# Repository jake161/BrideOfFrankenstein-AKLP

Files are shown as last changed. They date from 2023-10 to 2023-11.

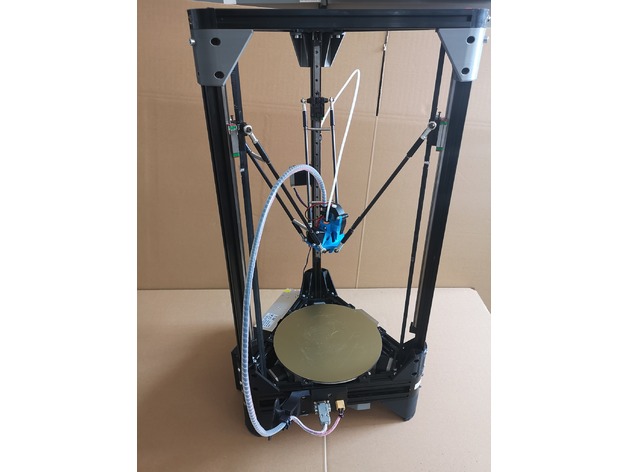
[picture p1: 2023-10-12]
STLs/Anycubic_Kossel_Linear_Plus__Light_weight_Effector_upgrade__E3D_V6__Volcano_too__and_5015_blower_4329200/images/featured_preview_95667094_4322474284432976_2573437162724786176_o.jpg

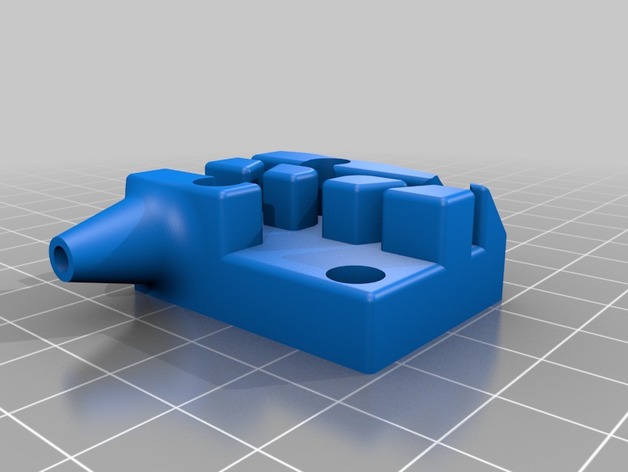
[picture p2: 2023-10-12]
STLs/Carriages_for_Anycubic_Delta_Kossel_Linear_Plus_2281894/images/Carriage_53mm.jpg

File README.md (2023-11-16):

# Bride of Frankenstein
## Anycubic Kossel Linear Plus Refresh and Klipper Conversion

_Everything here is work in progress, but hopefully it can be of some use!_

This repo is a dump/backup of my current Anycubic Kossel Klipper configuration which I affectionately call:

**Bride of Frankenstein (_BOF_)**

After swapping out the main board a few times, cannibalizing parts, and losing my configs, I had to cobble this monster back into something usable.

My current goal is to produce a bill of materials so that this machine can be reproduced. I believe the original Anycubic KLP was a great starter delta machine and hope it continues to get some use!

In pursuit of that goal, I've added some hardware and printable mods that really improve the experience. I'll include the STLs, and I'll try to properly credit and source their creators later on. Thank you for your work!

I've included the current printer.cfg, custom macros (a few of which are adopted from people on the klipper discord / lots of googling), and my PrusaSlicer configs.

## TODO:
- Create BOM for stock AKLP with quality of life upgrades (BOFV2)
- Create BOM for better start configuration with more substantial changes (BOFV3)

## CAD Attribution:

- [Original CAD by SPIKELEE](https://cults3d.com/:991294)

## STLs Attribution:

- [Improved Carriages (50mm version)](https://www.thingiverse.com/thing:2281894/files)
- [Upgraded Effector](https://www.thingiverse.com/thing:4329200)
- [Voron M4 Extruder](https://github.com/VoronDesign/Mobius-Extruder)
- [Glass Bed Clips](https://www.printables.com/model/137809-anycubic-kossel-linear-plus-glass-bed-clamp)
- [Corner Reinforcements](https://www.thingiverse.com/thing:2620272)
- [Top Mount Tensioners](https://www.thingiverse.com/thing:2827665)
- [Side Mounted Spool Holder](https://www.thingiverse.com/thing:2909802)

## Mods Currently in Use:

- [TMC2209s](https://www.amazon.com/BIGTREETECH-TMC2209-Stepper-Stepstick-Motherboard/dp/B07ZPYKL46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) _(I might post a guide for this since the resources I used in the past are outdated)_
- E3D V6 Clone _(Gulfcoast Robotics)_
- [Ultrabase](https://www.aliexpress.us/item/2251832729128038.html?gatewayAdapt=glo2usa4itemAdapt) _(I DO NOT recommend this bed, but it is currently what I am using. Adhesion sucks)_

## Macros worth pointing out:

- [PURGE_ARC](https://github.com/whyme12/Klipper_Macro_Collection)
- M600 _(If I can find the source I'll link it)_

## A few issues to note:

*Due to the modified effector I am currenty using, you can't use the fully radius of the build area. It's currently locked at R100mm for the Delta Radius, but delta calibrate says it's 134mm. To compensate, my PrusaSlicer profile is locked at D200mm. Also the PURGE_ARC macro has a 35mm offset to not exceed max dimensions.*

*Retraction is a bit out of whack at the moment. Currently running an Voron Mobius 4 Extruder on the worlds worst nema 17 (ripped from a tevo tarantula). My accel values are a bit off to not generate too much noise while printing. Although, I may try to drop retract speed even further. Update: I ran a slow retraction test. I believe the issue to actually be pressure advance. The filament travel is quite long so my PA values are really aggressive. I'll shorten it and retune.* 

*Tip: Something I learned the hard way is that you CANNOT use BED_MESH_CALIBRATE while running DELTA_CALIBRATE. Delta calibrate compensates for any innacuracies in your build by assuming a planar build surface. This means running a bed mesh will just exagerate imperfections and wildly throw off kinematics. (I've literally watched the effector fly away from the bed on the first layer)*

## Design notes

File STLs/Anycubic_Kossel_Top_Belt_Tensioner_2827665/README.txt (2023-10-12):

Anycubic Kossel Top Belt Tensioner by Atziano on Thingiverse: https://www.thingiverse.com/thing:2827665

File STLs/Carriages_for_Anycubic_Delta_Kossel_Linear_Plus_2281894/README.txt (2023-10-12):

Carriages for Anycubic Delta Kossel Linear Plus by theinternal on Thingiverse: https://www.thingiverse.com/thing:2281894

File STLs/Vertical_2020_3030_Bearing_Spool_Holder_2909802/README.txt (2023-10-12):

Vertical 2020/3030 Bearing Spool Holder by Hultis on Thingiverse: https://www.thingiverse.com/thing:2909802

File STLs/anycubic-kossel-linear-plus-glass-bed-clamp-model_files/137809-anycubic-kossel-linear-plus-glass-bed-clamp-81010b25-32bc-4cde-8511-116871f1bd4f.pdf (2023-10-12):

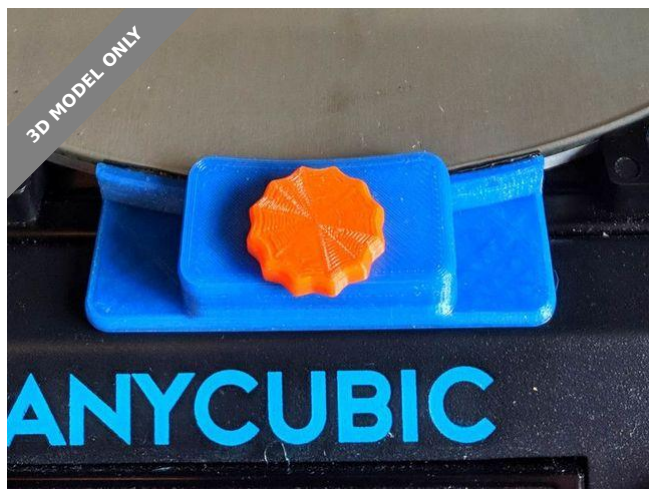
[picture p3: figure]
3D MODEL ONLY

# Summary

Update 27Jan20 In printing something wider than usual, I discovered that

the underside of my part cooling duct hit the...

3D Printers (https://www.printables.com/model?categoryId=1) | > | 3D Printers - Upgrades (https://www.printables.com/model?categoryId=2)
Tags: anycubickossel | linearplus | glassbedclamp

### Update 27Jan20

In printing something wider than usual, I discovered that the underside of

my part cooling duct hit the clamp bolt head on one of the side clamps (at

a radius of 110mm). I've redesigned the clamp bolt head to be a lever. This

alleviates two problems, firstly the width of the bolt head is less on the

build plate side of the clamp and a collision is less likely (not impossible - it

depends what you've set as your printable radius and which part cooling

duct you're using (I'm using Facocero's Thingiverse 3850300). If the

printable radius is less than 110mm, collision is avoided - the Anycubic

default seems to be 105mm), and secondly, David_J's problem of the bolt

being a little too tight to undo comfortably, because now the bolt head is

the shape of a small spanner / wrench and gives a little extra leverage. As

a feature, when tightened, the lever parks with its protruberance

perpendicular to the build plate, as shown in the photo. This is now version

## PeterH1500 (https://www.printables.com/social/222565/about)

# Anycubic Kossel Linear Plus Glass Bed Clamp

VIEW IN BROWSER (https://www.printables.com/model/137809-anycubic-kossel-linear-plus-glass-bed-clamp)

updated 12. 4. 2022 | published 22. 2. 2022

1.2, which I printed 3 bolts at a time in orange Sunlu PLA+ with 0.2mm

layers (0.5mm nozzle), 3 perimeters and 10% infill.

### Update 13Nov19

Following from David_J's comment about the clamp screw being difficult to

unscrew, I've produced a design for a small spanner / wrench for those

who have this difficulty. I've printed this in silver Sunlu PLA+ with 0.25mm

layers (0.5mm nozzle), 5 perimeters and 20% infill.

### Update 21Oct19:

I have extended the fixing bolt holes to allow additional, tighter

adjustment towards the build plate (an additional 0.925mm). This is now

version 1.1, and the Onshape link will now take you to this version.

Initial version 31Jul19:

I hadn't found a suitable clamp to hold my borosilicate glass build plate on

my heated bed, so I set about designing one from scratch. I used Onshape

for the original drawing, so if you want to do any adjustments to the

original drawings you can find them with this link:

https://cad.onshape.com/documents/ec0d91ee24f4f9e61d9240a1/w/

4435b4504876d0c24c086cef/e/5444b0fb228acd7783f3b459 (https://cad.onshape.com/documents/ec0d91ee24f4f9e61d9240a1/w/4435b4504876d0c24c086cef/e/5444b0fb228acd7783f3b459)

The Anycubic Kossel Linear Plus has a 240mm diameter build plate held in

place on a triangle formed from 2020 profile aluminium extrusion.

I regularly use my heated build plate at 70°C, so I printed the clamp in

PETG because of it's higher temperature tolerance when compared to PLA

(glass transition at about 80°C versus 60-65°C, but also added a silicone

gasket in the form of self-amalgamating tape, to help insulate the PETG,

just in case I want to use a bed temperature higher than 80°C. I glued this

in place with a clear impact adhesive. If you use the same stuff, don't

allow your gaskets to touch or they will amalgamate and prevent you

removing your clamp!

I printed the clamp bolt/screw in Sunlu PLA+ because the threads are

better defined than with PETG, and the screw doesn't touch anything hot

and so won't melt or distort.

As well as the printed parts, you'll need 2 off M3 x 8mm socket button

screws (these fit in the recess) and M3 T-nuts for each clamp.

# Print Settings

## Printer:

# Model files

Anycubic Kossel Linear Plus (Delta)

## Rafts:

No

## Supports:

No

## Resolution:

0.2mm first layer then 0.15mm

## Infill:

25%

### Filament: Esun (PETG) & Sunlu (PLA+) PETG (blue) & PLA+ (orange)

## Notes:

The degree of infill doesn't appear to be critical.

Category: 3D Printer Parts

## clamp.stl

## spanner.stl

## clamp_bolt.stl

## clamp_bolt_v12.stl

Find source .stl files on Thingiverse.com (https://www.thingiverse.com/thing:3781497)

# License

This work is licensed under a

Creative Commons (4.0 International License)

Attribution—Noncommercial—Share Alike (http://creativecommons.org/licenses/by-nc-sa/4.0/)

### ✖ | Sharing without ATTRIBUTION

✔ | Remix Culture allowed
✖ | Commercial Use
✖ | Free Cultural Works
✖ | Meets Open Definition

## clamp_base_v11.stl

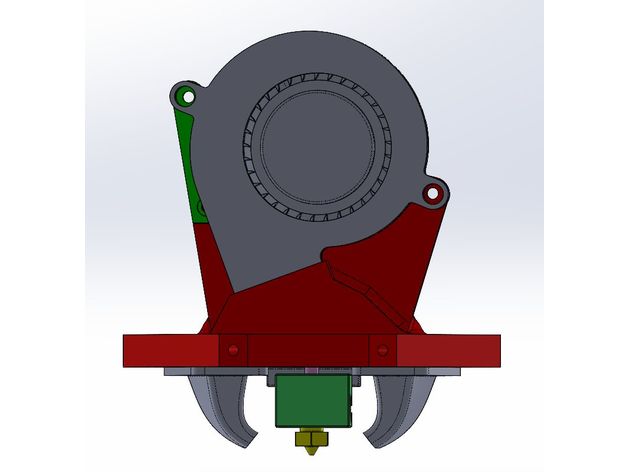
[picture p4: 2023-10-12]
STLs/Anycubic_Kossel_Linear_Plus__Light_weight_Effector_upgrade__E3D_V6__Volcano_too__and_5015_blower_4329200/images/featured_preview_2.jpg

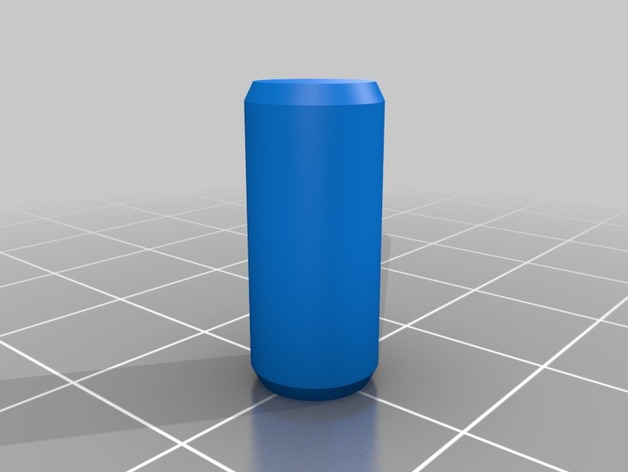
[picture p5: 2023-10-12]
STLs/Vertical_2020_3030_Bearing_Spool_Holder_2909802/images/Pin.jpg

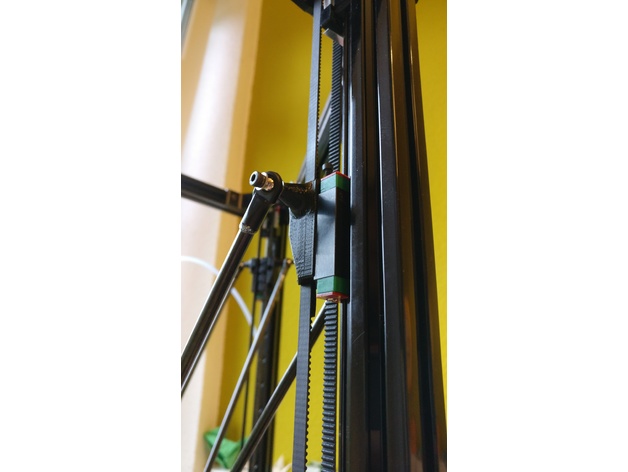
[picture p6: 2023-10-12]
STLs/Carriages_for_Anycubic_Delta_Kossel_Linear_Plus_2281894/images/ce06621213bb93edf30e082a9b9ab08d.jpg

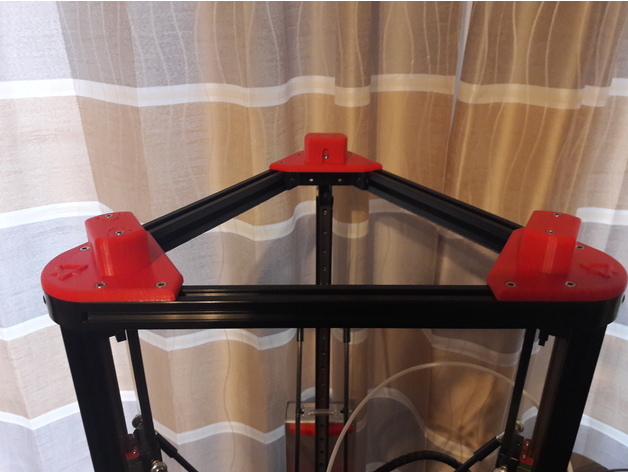
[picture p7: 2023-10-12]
STLs/Anycubic_Kossel_Top_Belt_Tensioner_2827665/images/1eb0ceaca3b0e80c4a3fc1027c2ebc53.jpg

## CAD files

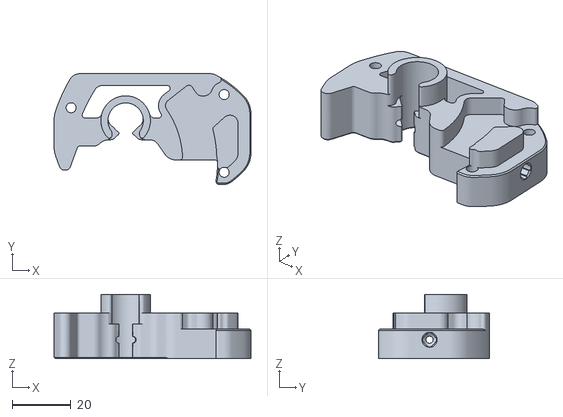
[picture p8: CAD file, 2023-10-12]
STLs/Mobius-Extruder-M4/Mobius-Extruder-M4/STLs/main_body_mirror.stl
66.8 x 37.6 x 21.8

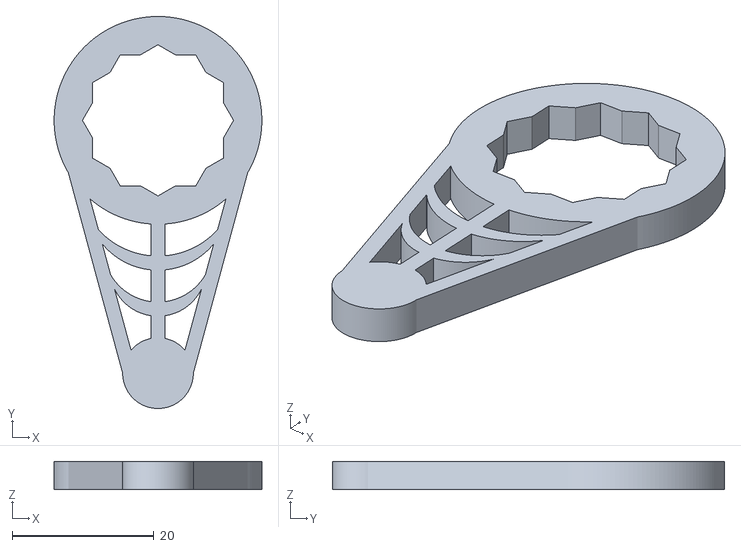
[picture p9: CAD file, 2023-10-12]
STLs/anycubic-kossel-linear-plus-glass-bed-clamp-model_files/spanner.stl
29.4 x 55.4 x 4.00

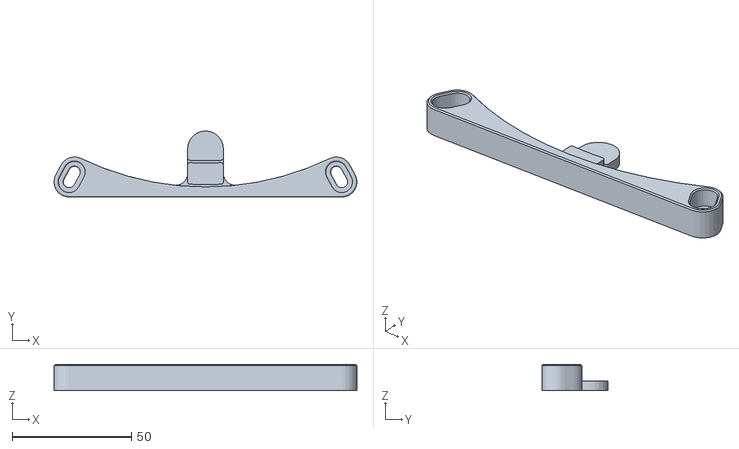
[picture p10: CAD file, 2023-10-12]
STLs/anycubic-kossel-plus-heated-bed-clips-3d-model/files/Anycubic_Plus_Bed_Clip.stl
127.0 x 27.8 x 11.0

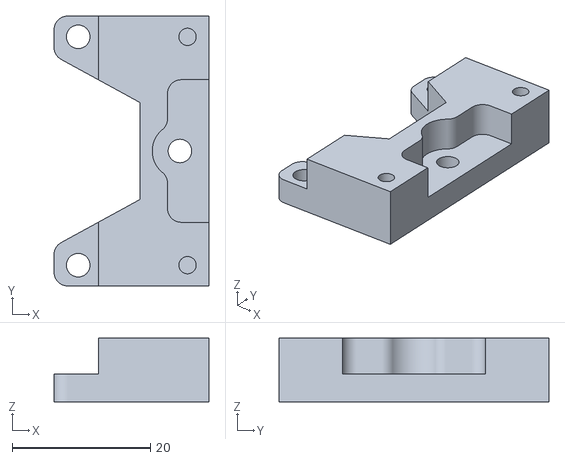
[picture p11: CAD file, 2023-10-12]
STLs/Anycubic_Kossel_Linear_Plus__Light_weight_Effector_upgrade__E3D_V6__Volcano_too__and_5015_blower_4329200/files/volcano_offset_holder_sensor.STL
22.4 x 39.0 x 9.20

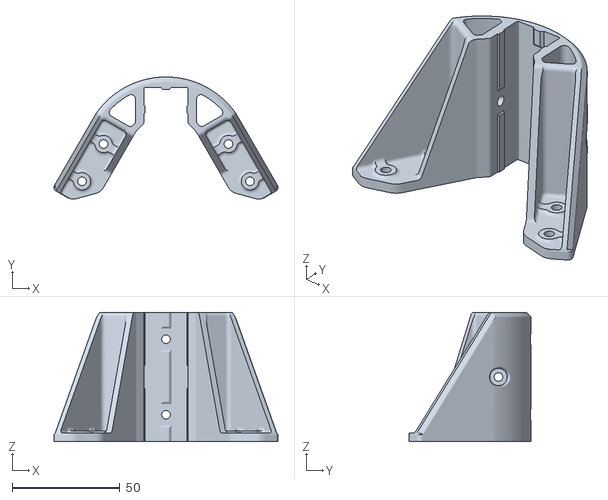
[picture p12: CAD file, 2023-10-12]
STLs/Anycubic_Kossel_Plus_Reinforcement_Corner_-_Escuadr_n_2620272/files/Escuadron_1hole.STL
103.9 x 56.6 x 60.0

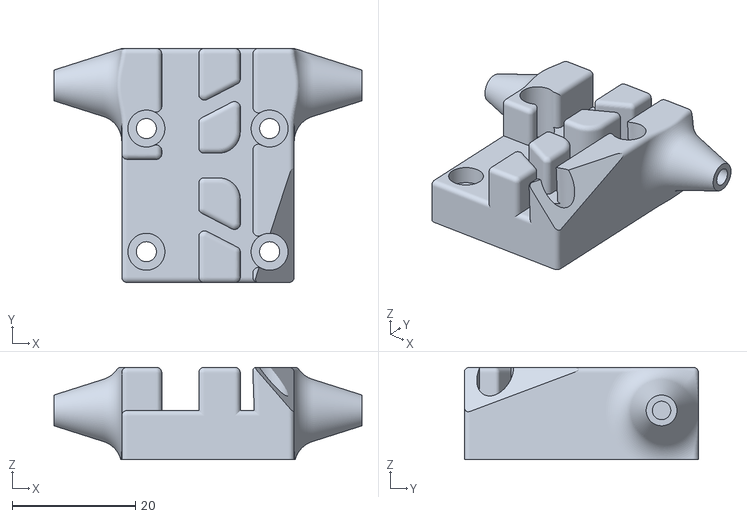
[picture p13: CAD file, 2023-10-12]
STLs/Carriages_for_Anycubic_Delta_Kossel_Linear_Plus_2281894/files/Carriage_50mm.stl
50.0 x 38.0 x 15.0

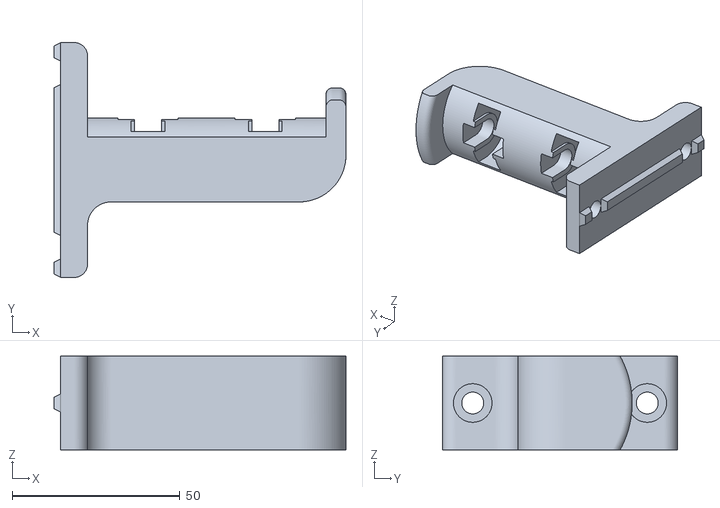
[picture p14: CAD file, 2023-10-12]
STLs/Vertical_2020_3030_Bearing_Spool_Holder_2909802/files/3030_spool_holder.stl
87.0 x 70.0 x 28.0

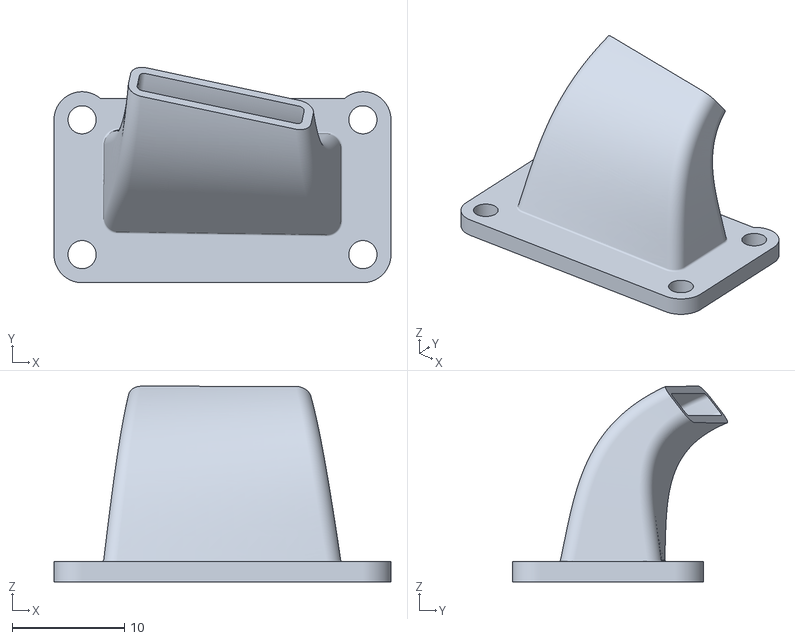
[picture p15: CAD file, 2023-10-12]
STLs/Anycubic_Kossel_Linear_Plus__Light_weight_Effector_upgrade__E3D_V6__Volcano_too__and_5015_blower_4329200/files/fan_jet_L.STL
30.0 x 19.2 x 17.4

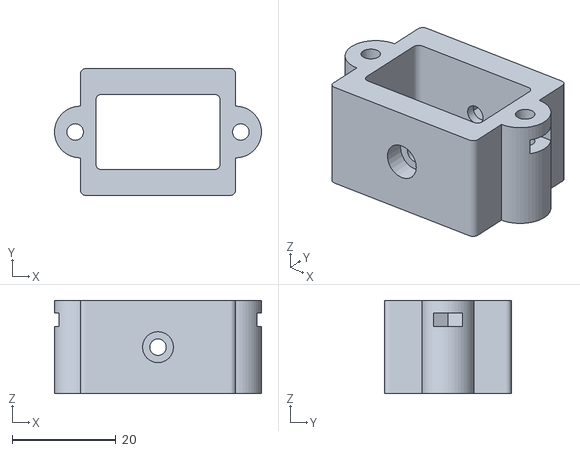
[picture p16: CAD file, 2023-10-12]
STLs/Anycubic_Kossel_Top_Belt_Tensioner_2827665/files/Slider.stl
40.0 x 24.5 x 18.1

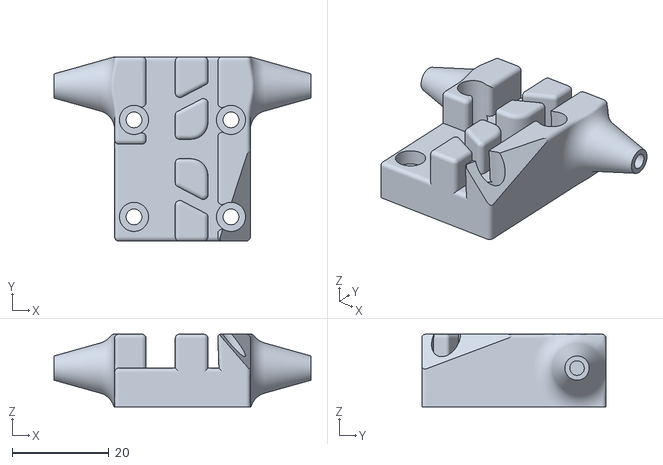
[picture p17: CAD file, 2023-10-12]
STLs/Carriages_for_Anycubic_Delta_Kossel_Linear_Plus_2281894/files/Carriage_53mm.stl
53.0 x 38.0 x 15.0

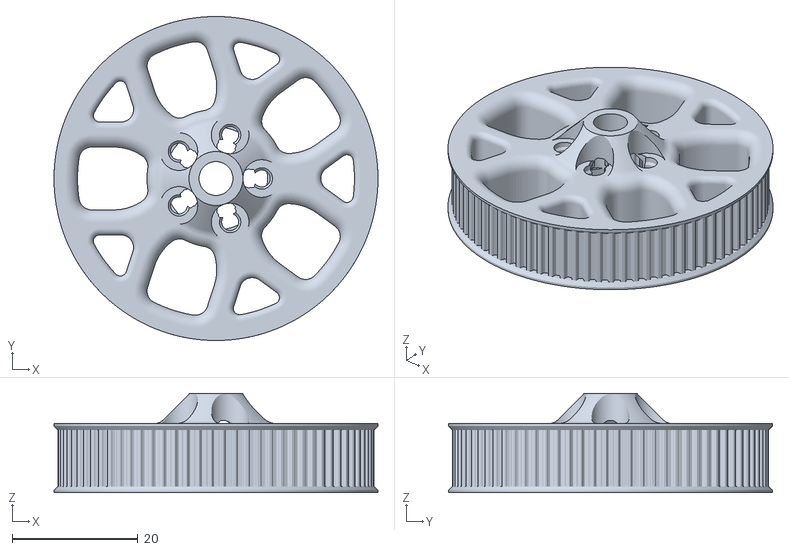
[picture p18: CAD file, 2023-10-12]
STLs/Mobius-Extruder-M4/Mobius-Extruder-M4/STLs/[a]_80t_gear.stl
51.6 x 51.6 x 15.8

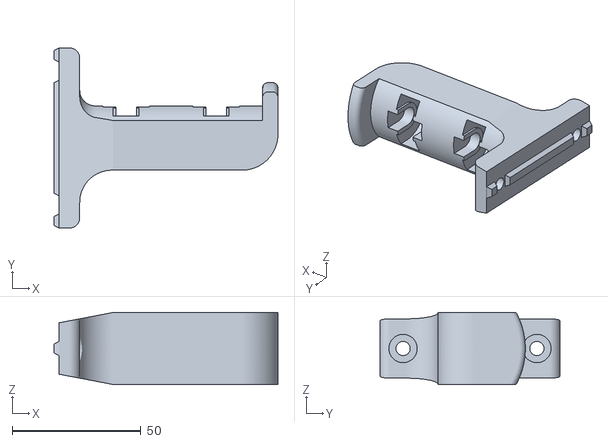
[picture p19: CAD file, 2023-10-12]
STLs/Vertical_2020_3030_Bearing_Spool_Holder_2909802/files/2020_spool_holder.stl
87.0 x 70.0 x 28.0

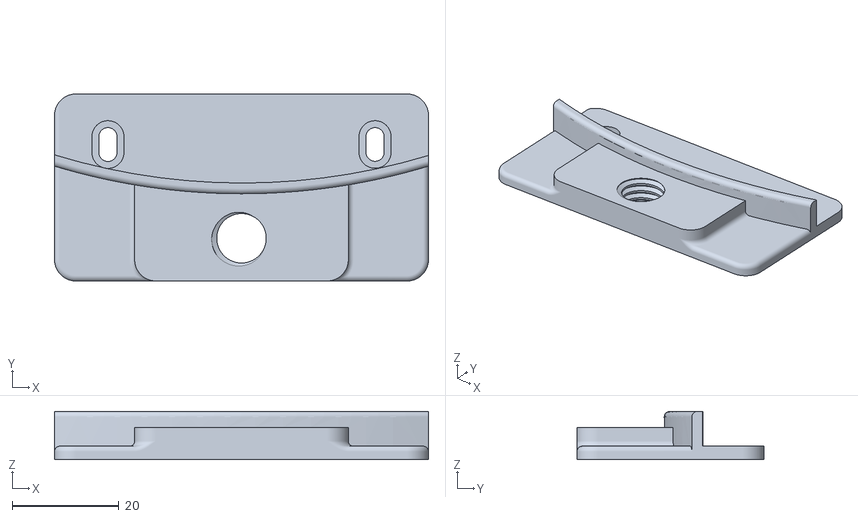
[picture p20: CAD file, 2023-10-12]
STLs/anycubic-kossel-linear-plus-glass-bed-clamp-model_files/clamp_base_v11.stl
70.0 x 35.0 x 9.00

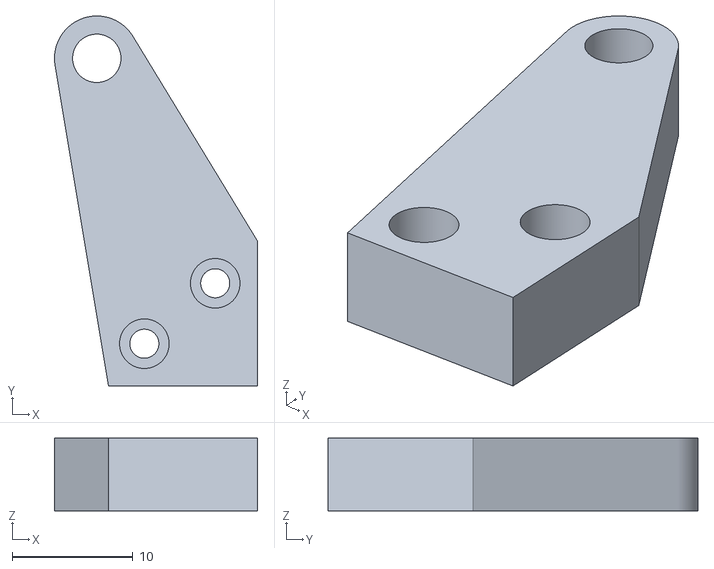
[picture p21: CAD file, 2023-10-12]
STLs/Anycubic_Kossel_Linear_Plus__Light_weight_Effector_upgrade__E3D_V6__Volcano_too__and_5015_blower_4329200/files/5015_blower_holderWithBigger4mmHole.STL
16.8 x 30.6 x 6.00

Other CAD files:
STLs/Mobius-Extruder-M4/Mobius-Extruder-M4/STLs/main_body.stl
STLs/Anycubic_Kossel_Plus_Reinforcement_Corner_-_Escuadr_n_2620272/files/Escuadron_simple_V2.STEP
STLs/Anycubic_Kossel_Plus_Reinforcement_Corner_-_Escuadr_n_2620272/files/Escuadron_2hole.STL
STLs/Anycubic_Kossel_Top_Belt_Tensioner_2827665/files/TopcoverV1.1.stl
STLs/Anycubic_Kossel_Linear_Plus__Light_weight_Effector_upgrade__E3D_V6__Volcano_too__and_5015_blower_4329200/files/5015_blower_holder.STL
STLs/Anycubic_Kossel_Linear_Plus__Light_weight_Effector_upgrade__E3D_V6__Volcano_too__and_5015_blower_4329200/files/fan_jet_R.STL
STLs/Anycubic_Kossel_Linear_Plus__Light_weight_Effector_upgrade__E3D_V6__Volcano_too__and_5015_blower_4329200/files/u_horseshoe.STL
STLs/Anycubic_Kossel_Plus_Reinforcement_Corner_-_Escuadr_n_2620272/files/Escuadron_simple_v2.STL
STLs/Anycubic_Kossel_Top_Belt_Tensioner_2827665/files/TopcoverV1.0.stl
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

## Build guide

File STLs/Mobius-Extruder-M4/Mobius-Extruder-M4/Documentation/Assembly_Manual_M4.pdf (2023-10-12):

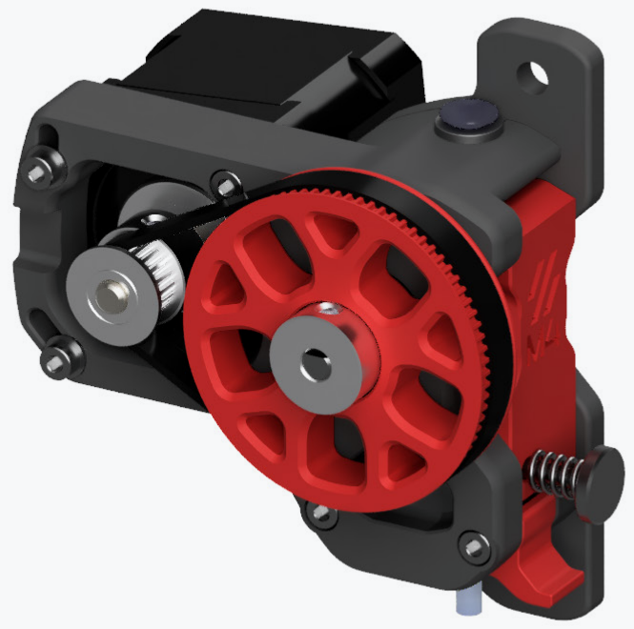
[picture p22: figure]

1

### WWW.VORONDESIGN.COM

VERSION 2020-10-19

# M4 ASSEMBLY MANUAL

## We build space shuttles with gardening tools

so anyone can have a space shuttle of their own.

# VORON

2

INTRODUCTION | WWW.VORONDESIGN.COM

Before you begin on your journey, a word of caution.

In the comfort of your own home you are about to assemble a robot. This
machine can maim, burn, and electrocute you if you are not careful. Please
do not become the first VORON fatality. There is no special Reddit flair for that.

Please, read the entire manual before you start assembly. As you begin wrenching, please check our Discord channels for any tips and questions that may halt your progress.

Most of all, good luck!
THE VORON TEAM

3

INTRODUCTION | WWW.VORONDESIGN.COM

PART PRINTING GUIDELINES
The Voron Team has provided the following print guidelines for you to follow in order to have the best chance at success with your parts. There are often questions about substituting materials or changing printing standards, but we recommend you follow these.

3D PRINTING PROCESS
Fused Deposition Modeling (FDM)

MATERIAL
ABS

LAYER HEIGHT
Recommended: 0.2mm

EXTRUSION WIDTH
Recommended: Forced 0.4mm

INFILL TYPE
Grid, Gyroid, Honeycomb, Triangle or Cubic

INFILL PERCENTAGE
Recommended: 40%

WALL COUNT
Recommended: 4

SOLID TOP/BOTTOM LAYERS
Recommended: 5

PRINT IT FORWARD (PIF)
Often times our community members have issues printing ABS will bootstrap themselves into a VORON using our Print It Forward program. This is a service where approved members with VORON printers can make you a functional set of parts to get your own machine up and running.
Check Discord if you have any interest in having someone help you out.

4

INTRODUCTION | WWW.VORONDESIGN.COM

HOW TO GET HELP
If you need assistance with your build, we’re here to help. Head on over to our Discord group and post your questions. This is our primary medium to help VORON Users and we have a great community that can help you out if you get stuck.

https://discord.gg/voron

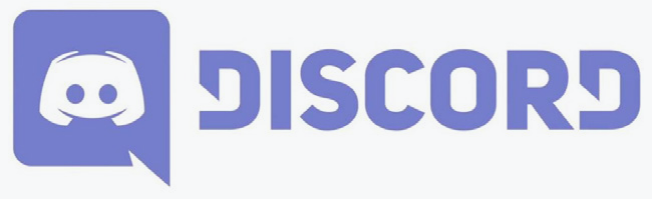
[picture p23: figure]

THIS IS JUST A REFERENCE
This manual is designed to be a simple reference manual. Building a Voron can be a complex endeavour and for that reason we recommend downloading the CAD files off our Github repository if there are sections you need clarification on. It can be sometimes be easier to follow along when you have the whole assembly in front of you.

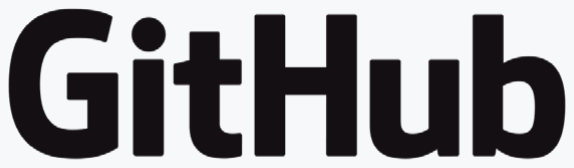
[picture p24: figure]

https://github.com/vorondesign

5

### WWW.VORONDESIGN.COM

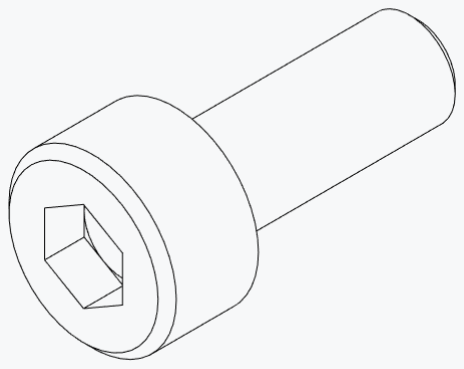
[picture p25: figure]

SOCKET HEAD CAP SCREW (SHCS) Metric fastener with a cylindrical head and hex drive. The most common fastener used on the Voron.

ISO 4762

WASHER
Small metal disc to increase the surface area.

DIN 988

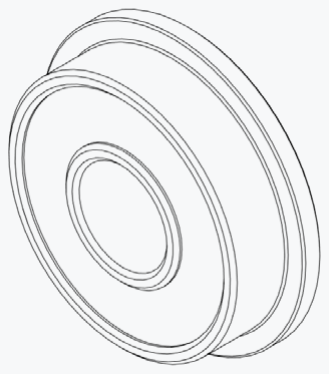
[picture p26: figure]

PULLEY
GT2 pulley used on the motion system of the Voron.

HARDWARE
HEAT SET INSERT
Heat inserts with a soldering tip so that they melt the plastic when installed. As the plastic cools, it solidifies around the knurls and ridges on the insert for excellent resistance to both torque and pull-out.

F695 BEARING
A ball bearing with a flange used in various gantry locations.

GRUB SCREW
Small headless screw with an internal drive.

ISO 4026

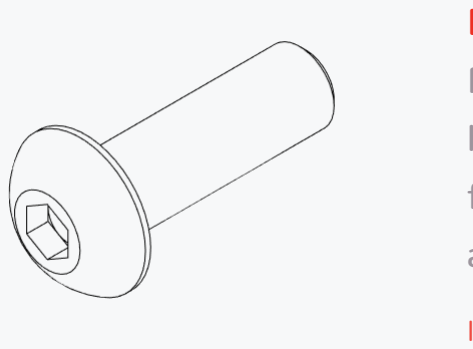
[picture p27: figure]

BUTTON HEAD CAP SCREW (BHCS) Metric fastener with a domed shape head and hex drive. Most commonly found in locations where M5 fasteners are used.

ISO 7380-1

### WWW.VORONDESIGN.COM

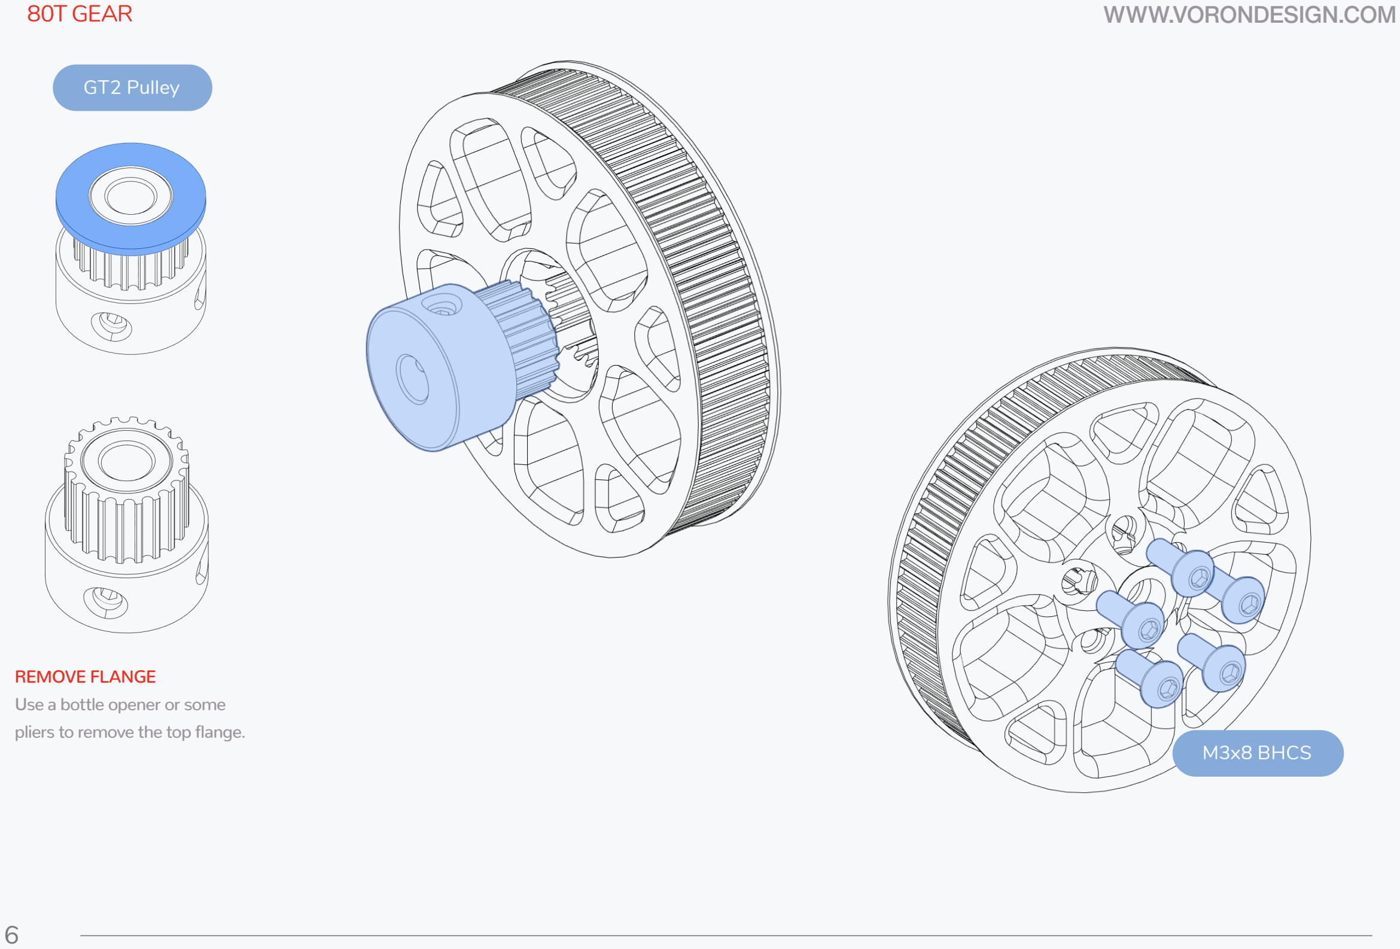
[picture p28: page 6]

6

REMOVE FLANGE
Use a bottle opener or some pliers to remove the top flange.

GT2 Pulley

M3x8 BHCS

80T GEAR

7

### WWW.VORONDESIGN.COM

CHECK BEARING FIT
The bearings must slip on and off the shaft easily. Pressing the bearings on the shaft will damage them. Lightly sand the shaft if required.

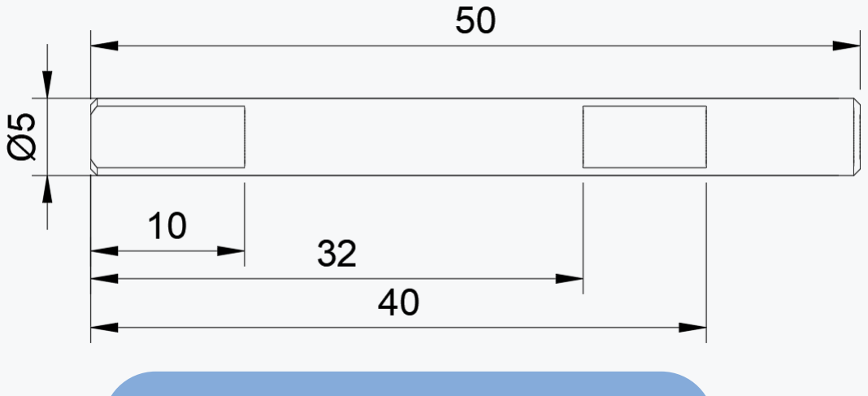
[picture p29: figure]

5x50mm Shaft w/ Flats
F695 Bearing

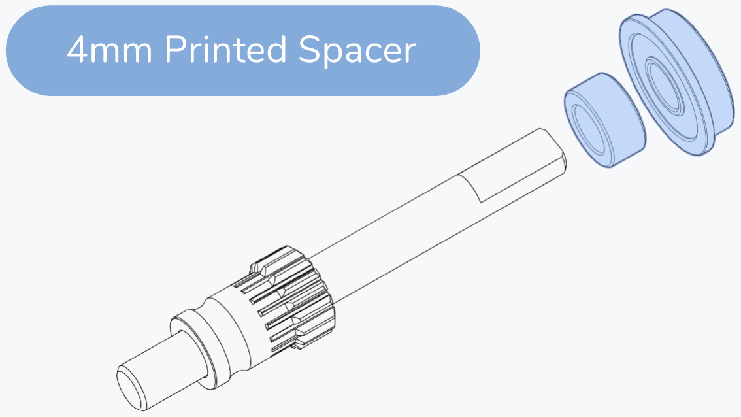
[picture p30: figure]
4mm Printed Spacer

DRIVE GEAR POSITION
Position the drive gear 8mm from the end of the shaft and tighten the grub screw.
Use thread locker.

DRIVE SHAFT

FLAT FACE ON THE SHAFT
Align the flat face of the shaft with the grub screw of the drive gear. If your shaft is fully round make a small flat spot with a file to ensure proper seating.

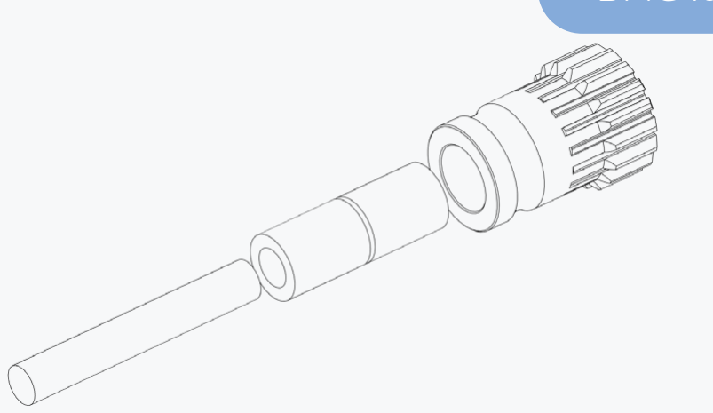
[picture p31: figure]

8

### WWW.VORONDESIGN.COM

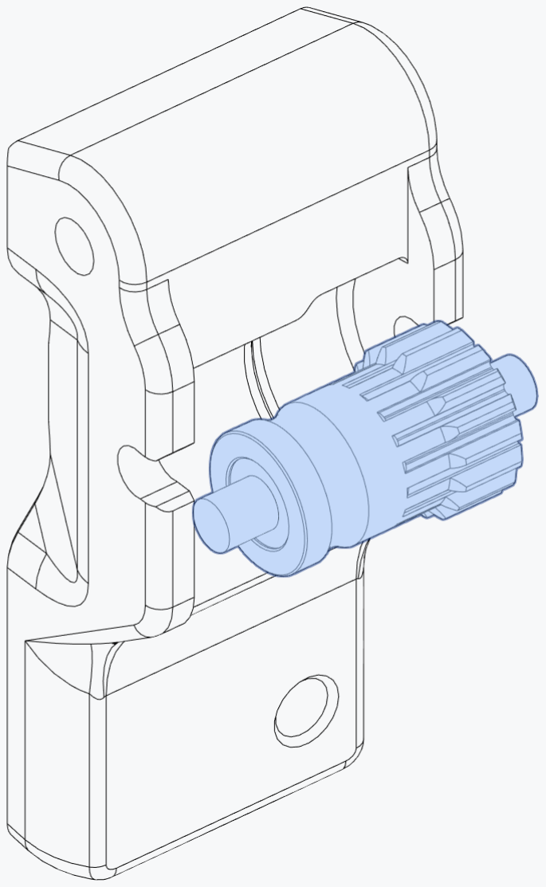
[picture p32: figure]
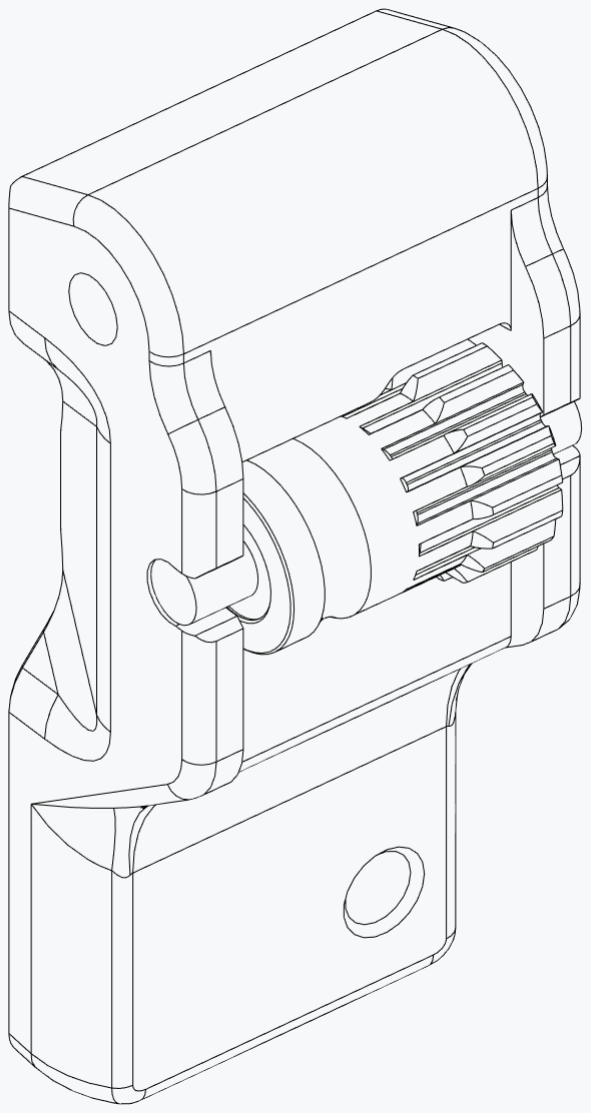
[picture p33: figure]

LUBRICATE BEARINGS
A light lubrication film will help with smooth operation and longevity.

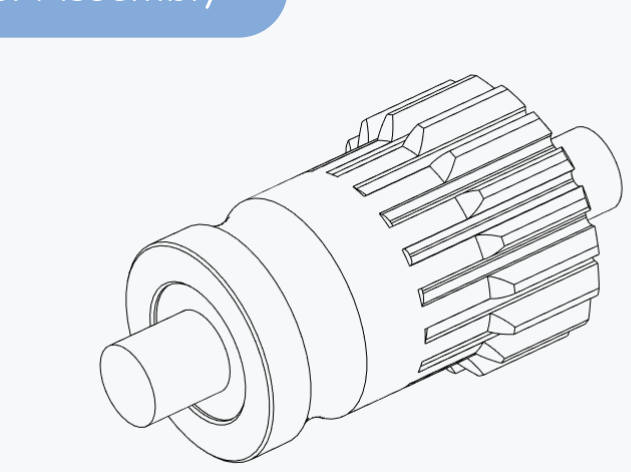
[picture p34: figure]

BMG Idler Assembly

IDLER ASSEMBLY

### WWW.VORONDESIGN.COM

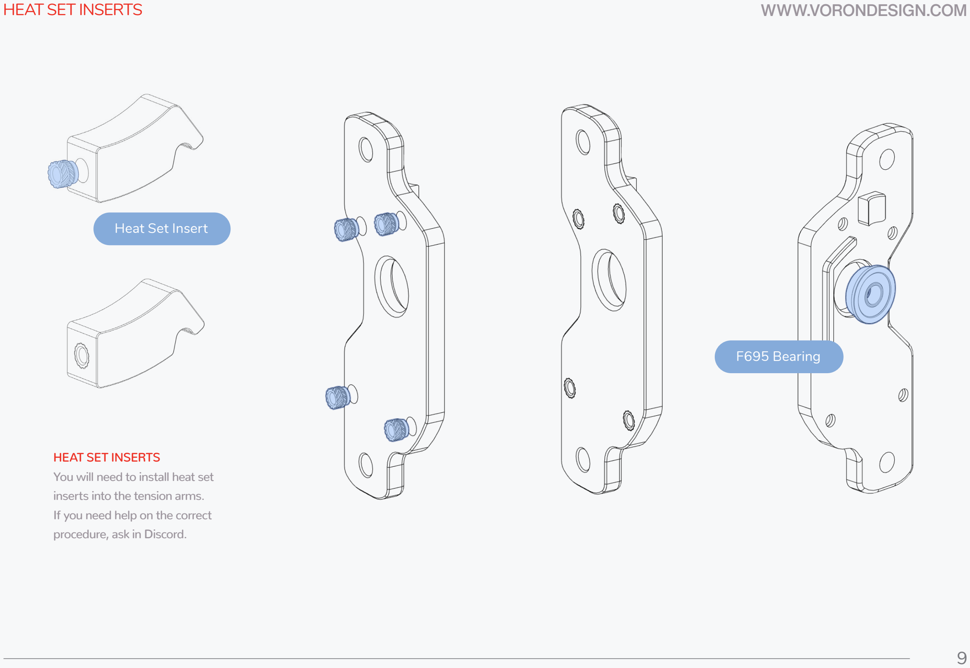
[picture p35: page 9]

9

HEAT SET INSERTS
You will need to install heat set inserts into the tension arms. If you need help on the correct procedure, ask in Discord.

Heat Set Insert

F695 Bearing

HEAT SET INSERTS

BODY ASSEMBLY | WWW.VORONDESIGN.COM

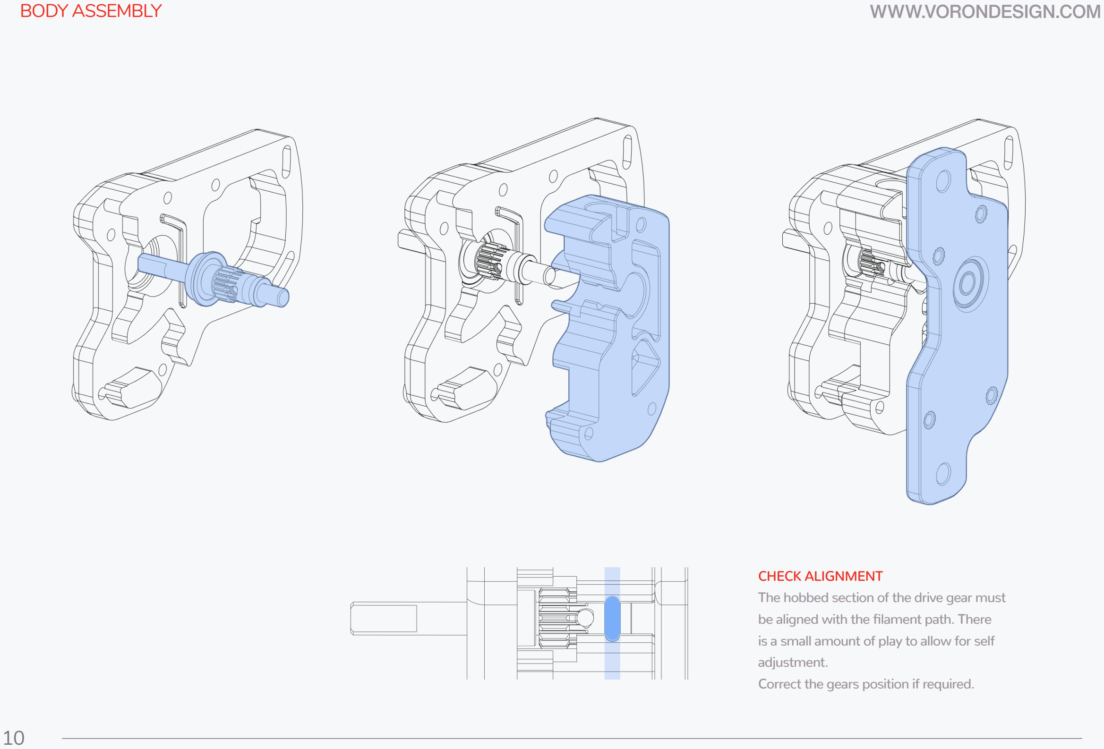
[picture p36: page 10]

10

CHECK ALIGNMENT
The hobbed section of the drive gear must be aligned with the filament path. There is a small amount of play to allow for self adjustment.
Correct the gears position if required.

BODY ASSEMBLY | WWW.VORONDESIGN.COM

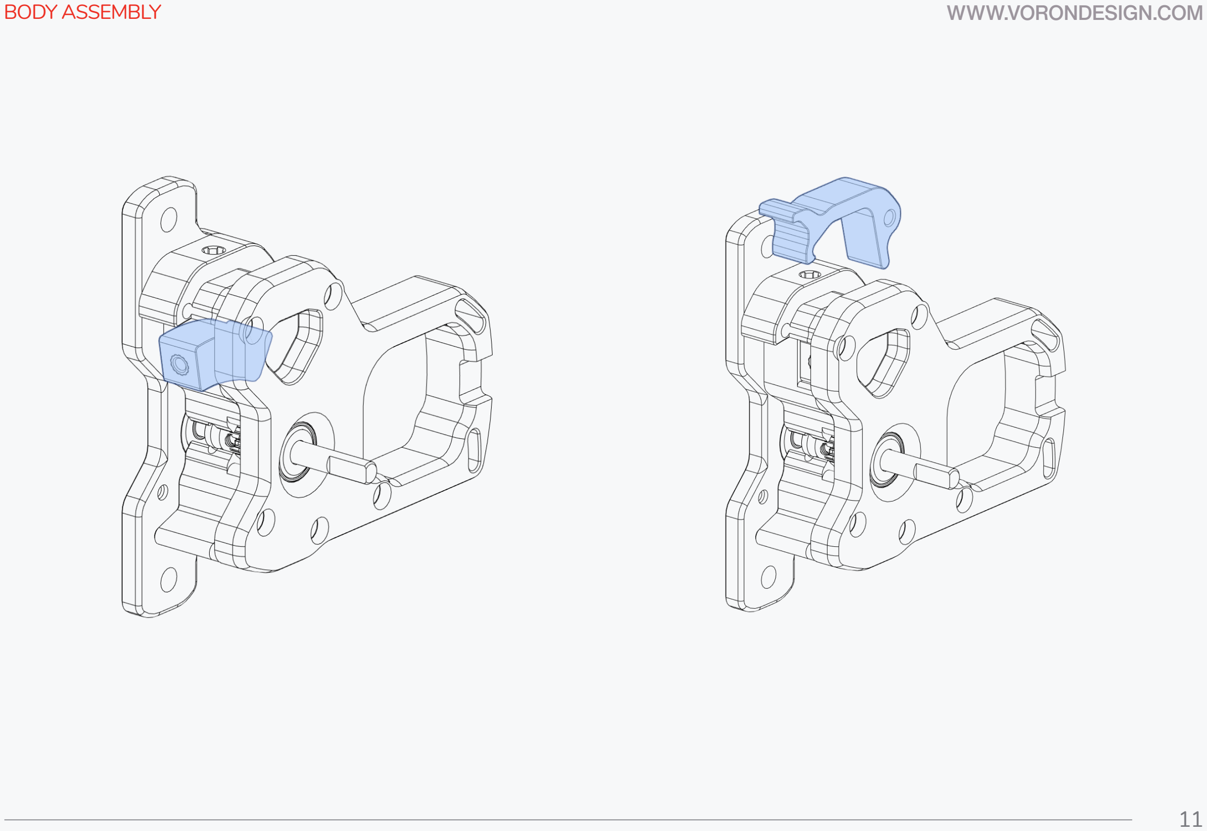
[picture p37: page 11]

11

12

### WWW.VORONDESIGN.COM

BODY ASSEMBLY

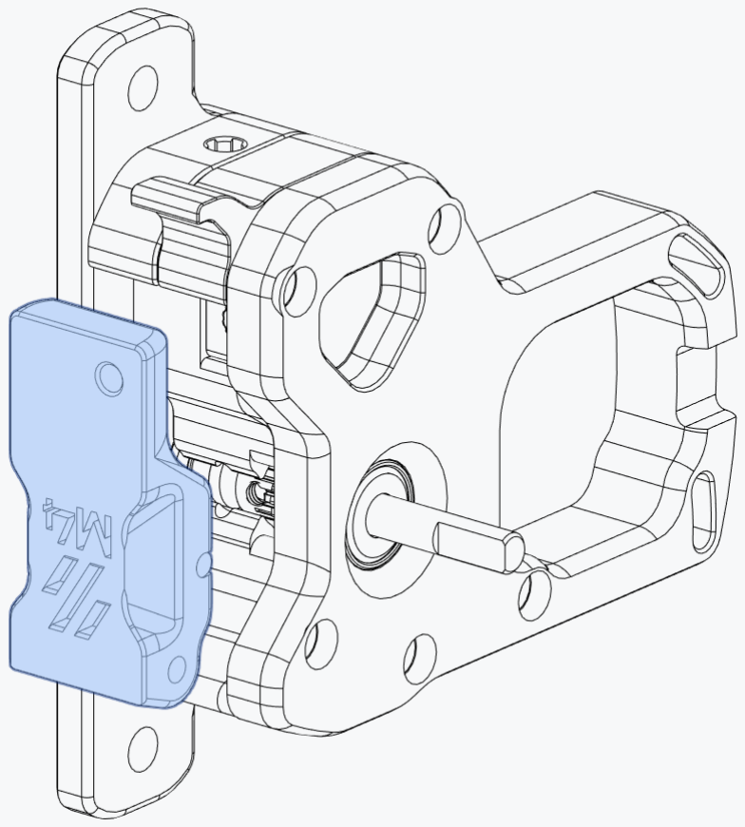
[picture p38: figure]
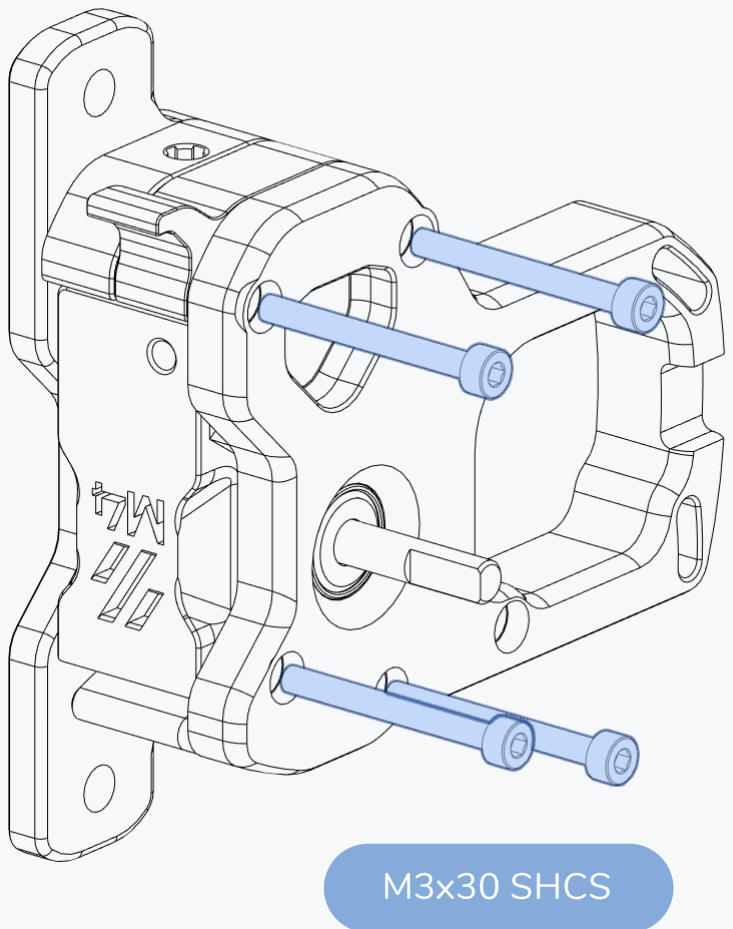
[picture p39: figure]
M3x30 SHCS

### WWW.VORONDESIGN.COM

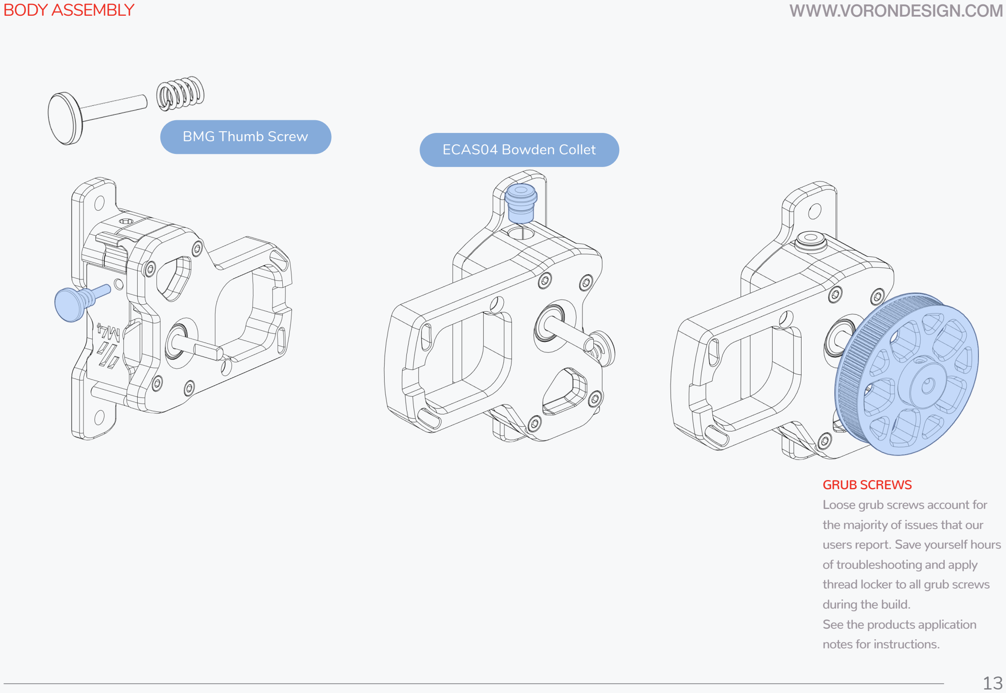
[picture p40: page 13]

13

GRUB SCREWS
Loose grub screws account for the majority of issues that our users report. Save yourself hours of troubleshooting and apply thread locker to all grub screws during the build.
See the products application notes for instructions.

BMG Thumb Screw
ECAS04 Bowden Collet

BODY ASSEMBLY

### WWW.VORONDESIGN.COM

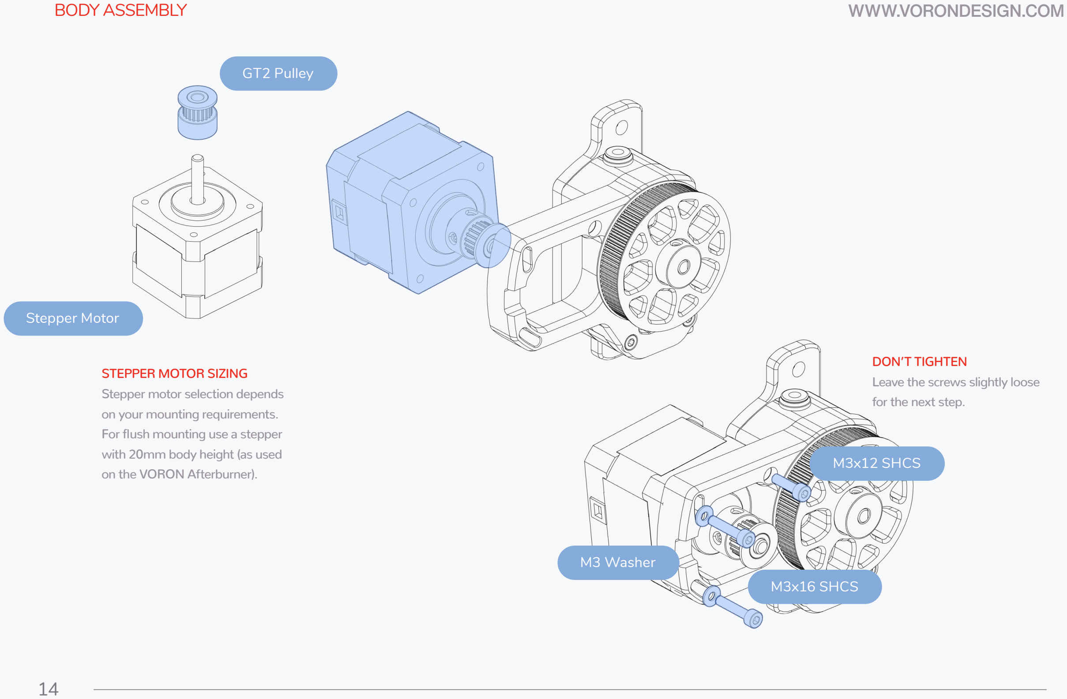
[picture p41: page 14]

14

GT2 Pulley

Stepper Motor

STEPPER MOTOR SIZING
Stepper motor selection depends on your mounting requirements. For flush mounting use a stepper with 20mm body height (as used on the VORON Afterburner).

M3x12 SHCS

M3x16 SHCS

M3 Washer

DON’T TIGHTEN
Leave the screws slightly loose for the next step.

BODY ASSEMBLY

15

### WWW.VORONDESIGN.COM

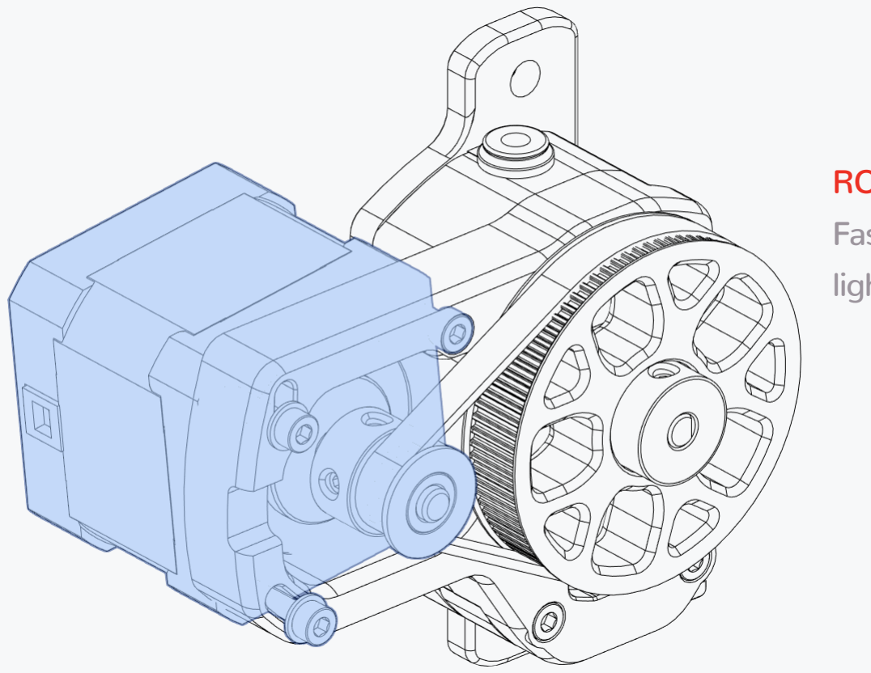
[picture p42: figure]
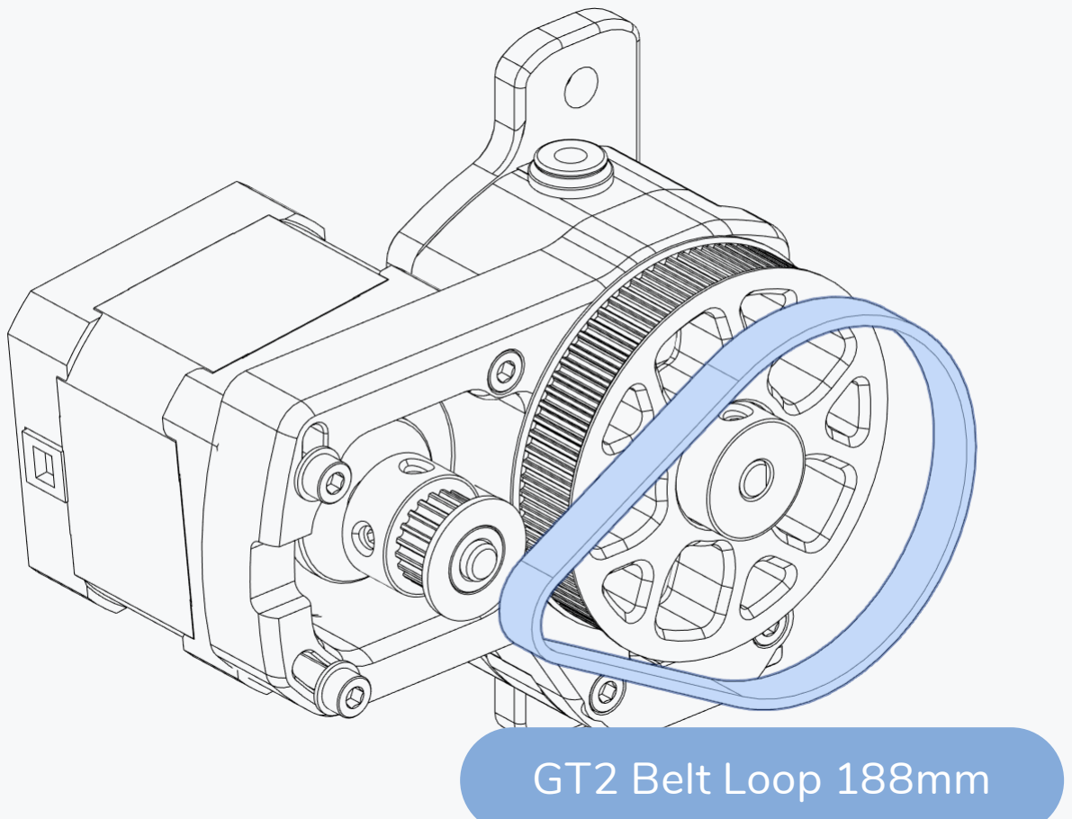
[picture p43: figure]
GT2 Belt Loop 188mm

ROTATE STEPPER TO TIGHTEN
Fasten the screws after applying a light pressure to tighten the belt.

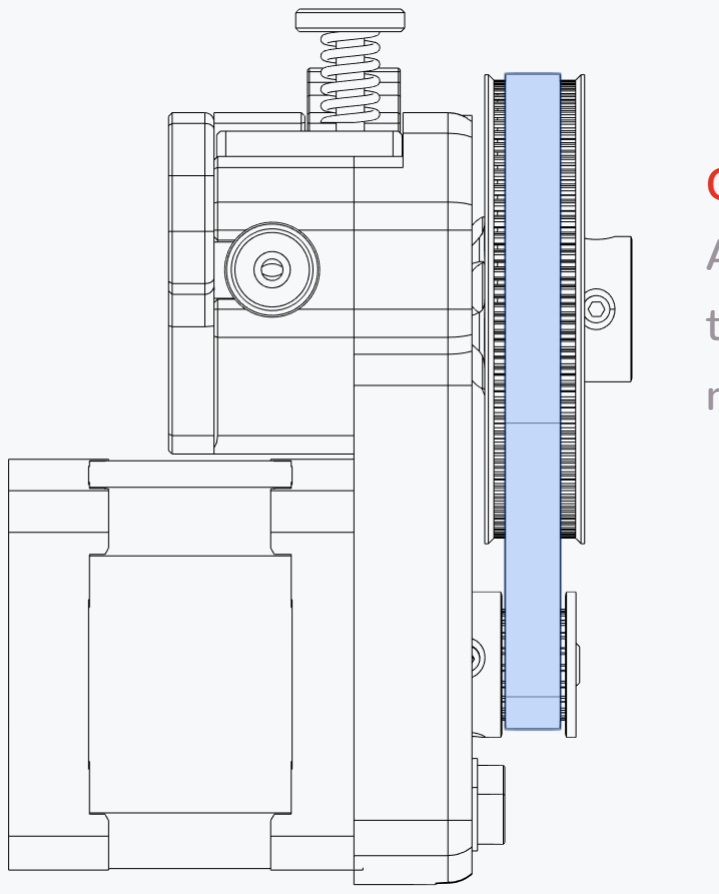
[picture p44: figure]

CHECK ALIGNMENT
Adjust the position of the pulley on the stepper if required. Belt must not rub on the flanges.

DRIVE BELT & ALIGNMENT

16

### WWW.VORONDESIGN.COM

Github
https://github.com/vorondesign

Website
www.vorondesign.com

Discord
https://discord.gg/voron

# VORON

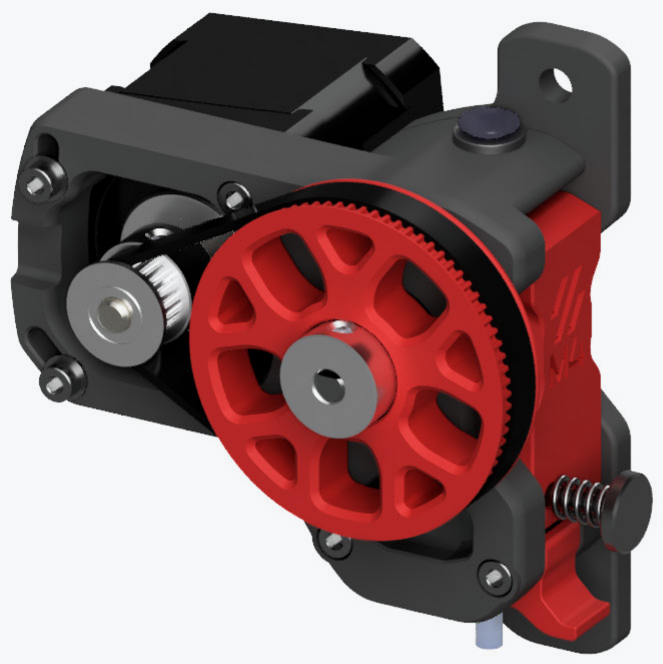
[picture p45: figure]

17

### WWW.VORONDESIGN.COM

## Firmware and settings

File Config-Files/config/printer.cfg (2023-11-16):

[include Macros/MAINSAIL_MACROS.cfg]
[include Macros/CUSTOM_MACROS.cfg]
[include Macros/TEST_SPEED_DELTA.cfg]
[include Macros/PURGE_ARC.cfg]
[include Macros/TUNING_TOWERS.cfg]
#[include adxl.cfg]
#[include Macros/reshelper.cfg]

# OG Trigorilla Board v1.1
# To use this config, the firmware should be compiled for the AVR atmega2560.
# 0.5 PA for PETG was immaculate, but top layers suffered. fix retraction regardless
# See docs/Config_Reference.md for a description of parameters.

[virtual_sdcard]
path: /home/jake_161/printer_data/gcodes
on_error_gcode: CANCEL_PRINT

[mcu]
serial: /dev/serial/by-id/usb-Silicon_Labs_CP2102_USB_to_UART_Bridge_Controller_0001-if00-port0

[stepper_a]
step_pin: PF0
dir_pin: PF1
enable_pin: !PD7
microsteps: 16
rotation_distance: 40
endstop_pin: ^PJ1
homing_speed: 100

#This is required before your initial delta calibrate
#position_endstop: 270
#arm_length: 269.0

[tmc2209 stepper_a]
uart_pin: PB5
run_current: 1.0
stealthchop_threshold: 999999


[stepper_b]
step_pin: PF6
dir_pin: PF7
enable_pin: !PF2
microsteps: 16
rotation_distance: 40
endstop_pin: ^PJ0

[tmc2209 stepper_b]
uart_pin: PG5
run_current: 1.0
stealthchop_threshold: 999999


[stepper_c]
step_pin: PL3
dir_pin: PL1
enable_pin: !PK0
microsteps: 16
rotation_distance: 40
endstop_pin: ^PD2


[tmc2209 stepper_c]
uart_pin: PH3
run_current: 1.0
stealthchop_threshold: 999999


[extruder]
#Note: The rotation distance and gear_ratio are for a Voron M4 Extruder
step_pin: PA4
dir_pin: !PA6
enable_pin: !PA2
microsteps: 16
rotation_distance: 22.8234
gear_ratio: 80:20
nozzle_diameter: 0.400
filament_diameter: 1.750
heater_pin: PB4
sensor_type: EPCOS 100K B57560G104F
sensor_pin: PK5
#control: pid
#pid_Kp: 25.349
#pid_Ki: 1.216
#pid_Kd: 132.130
min_extrude_temp: 185
max_extrude_only_distance: 900
#max_extrude_only_velocity:
max_extrude_only_accel: 5000
min_temp: 0
max_temp: 275

[tmc2209 extruder]
uart_pin: PE3
run_current: 0.95
stealthchop_threshold: 999999

[heater_bed]
heater_pin: PH5
sensor_type: EPCOS 100K B57560G104F
sensor_pin: PK4
#control: pid
#pid_kp: 73.517
#pid_ki: 1.132
#pid_kd: 1193.728
min_temp: 0
max_temp: 90

[fan]
pin: PH6
kick_start_time: 0.200

[heater_fan extruder_cooler_fan]
pin: PH4

[probe]
pin: ^PD3
y_offset: 4.1
samples: 3

#[filament_switch_sensor my_sensor]
#switch_pin: !PE5

[printer]
kinematics: delta
max_velocity: 200
max_accel: 7500
max_z_velocity: 200
#delta_radius: 134.4 # For DELTA_CALIBRATE
minimum_z_position: -5

[delta_calibrate]
radius: 100
# If the original probe is used
horizontal_move_z: 20

[idle_timeout]
timeout: 18000 #360

[gcode_arcs]

[endstop_phase]

[firmware_retraction]
retract_length: 3.2
#   The length of filament (in mm) to retract when G10 is activated,
#   and to unretract when G11 is activated (but see
#   unretract_extra_length below). The default is 0 mm.
retract_speed: 20
#   The speed of retraction, in mm/s. The default is 20 mm/s.
unretract_extra_length: 0.5
#   The length (in mm) of *additional* filament to add when
#   unretracting.
unretract_speed: 20
#   The speed of unretraction, in mm/s. The default is 10 mm/s.

[input_shaper]
shaper_freq_x: 33.4
shaper_freq_y: 35.6
shaper_type: mzv
damping_ratio_x: 0.0656
damping_ratio_y: 0.0697

[exclude_object]

#*# <---------------------- SAVE_CONFIG ---------------------->
#*# DO NOT EDIT THIS BLOCK OR BELOW. The contents are auto-generated.
#*#
#*# [extruder]
#*# control = pid
#*# pid_kp = 24.367
#*# pid_ki = 1.269
#*# pid_kd = 116.959
#*#
#*# [probe]
#*# z_offset = 15.653
#*#
#*# [endstop_phase stepper_a]
#*# trigger_phase = 48/64
#*#
#*# [endstop_phase stepper_b]
#*# trigger_phase = 38/64
#*#
#*# [endstop_phase stepper_c]
#*# trigger_phase = 58/64
#*#
#*# [heater_bed]
#*# control = pid
#*# pid_kp = 75.814
#*# pid_ki = 1.089
#*# pid_kd = 1319.158
#*#
#*# [printer]
#*# delta_radius = 134.550883
#*#
#*# [stepper_a]
#*# angle = 209.442920
#*# arm_length = 269.000000
#*# position_endstop = 276.425367
#*#
#*# [stepper_b]
#*# angle = 329.630230
#*# arm_length = 269.000000
#*# position_endstop = 275.816870
#*#
#*# [stepper_c]
#*# angle = 90.000000
#*# arm_length = 269.000000
#*# position_endstop = 275.183134
#*#
#*# [delta_calibrate]
#*# height0 = 15.653
#*# height0_pos = 20867.333,20824.667,20746.333
#*# height1 = 15.653
#*# height1_pos = 25045.000,25090.667,18109.333
#*# height2 = 15.653
#*# height2_pos = 20161.000,27602.667,20075.667
#*# height3 = 15.653
#*# height3_pos = 18349.333,24324.000,24278.000
#*# height4 = 15.653
#*# height4_pos = 20125.333,20034.000,25387.000
#*# height5 = 15.653
#*# height5_pos = 23821.000,18468.667,23663.000
#*# height6 = 15.653
#*# height6_pos = 26509.333,20112.667,20010.333

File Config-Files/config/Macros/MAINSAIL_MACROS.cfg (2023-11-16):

## Mainsail client klipper macro definitions

[gcode_macro _CLIENT_VARIABLE]
variable_use_custom_pos   : True ; use custom park coordinates for x,y [True/False]
variable_custom_park_x    : 0.0   ; custom x position; value must be within your defined min and max of X
variable_custom_park_y    : 0.0   ; custom y position; value must be within your defined min and max of Y
variable_custom_park_dz   : 20.0   ; custom dz value; the value in mm to lift the nozzle when move to park position
variable_retract          : 1.0   ; the value to retract while PAUSE
variable_cancel_retract   : 5.0   ; the value to retract while CANCEL_PRINT
variable_speed_retract    : 35.0  ; retract speed in mm/s
variable_unretract        : 1.0   ; the value to unretract while RESUME
variable_speed_unretract  : 35.0  ; unretract speed in mm/s
variable_speed_hop        : 15.0  ; z move speed in mm/s
variable_speed_move       : 100.0 ; move speed in mm/s
variable_park_at_cancel   : False ; allow to move the toolhead to park while execute CANCEL_PRINT [True/False]
variable_park_at_cancel_x : None  ; different park position during CANCEL_PRINT [None/Position as Float]; park_at_cancel must be True
variable_park_at_cancel_y : None  ; different park position during CANCEL_PRINT [None/Position as Float]; park_at_cancel must be True
## !!! Caution [firmware_retraction] must be defined in the printer.cfg if you set use_fw_retract: True !!!
variable_use_fw_retract   : False ; use fw_retraction instead of the manual version [True/False]
variable_idle_timeout     : 0     ; time in sec until idle_timeout kicks in. Value 0 means that no value will be set or restored
gcode:

[pause_resume]

[display_status]

[respond]

[gcode_macro CANCEL_PRINT]
description: Cancel the actual running print
rename_existing: CANCEL_PRINT_BASE
gcode:
  ##### get user parameters or use default #####
  {% set client = printer['gcode_macro _CLIENT_VARIABLE']|default({}) %}
  {% set allow_park = client.park_at_cancel|default(false)|lower == 'true' %}
  {% set retract = client.cancel_retract|default(5.0)|abs %}
  ##### define park position #####
  {% set park_x = "" if (client.park_at_cancel_x|default(none) is none)
            else "X=" ~ client.park_at_cancel_x %}
  {% set park_y = "" if (client.park_at_cancel_y|default(none) is none)
            else "Y=" ~ client.park_at_cancel_y %}
  {% set custom_park = park_x|length > 0 or park_y|length > 0 %}
  ##### end of definitions #####
  # restore idle_timeout time if needed
  {% if printer['gcode_macro PAUSE'].restore_idle_timeout > 0 %}
    SET_IDLE_TIMEOUT TIMEOUT={printer['gcode_macro PAUSE'].restore_idle_timeout}
  {% endif %}
  {% if (custom_park or not printer.pause_resume.is_paused) and allow_park %} _TOOLHEAD_PARK_PAUSE_CANCEL {park_x} {park_y} {% endif %}
  _CLIENT_RETRACT LENGTH={retract}
  TURN_OFF_HEATERS
  M106 S0
  # clear pause_next_layer and pause_at_layer as preparation for next print
  SET_PAUSE_NEXT_LAYER ENABLE=0
  SET_PAUSE_AT_LAYER ENABLE=0 LAYER=0
  CANCEL_PRINT_BASE
  G28

[gcode_macro PAUSE]
description: Pause the actual running print
rename_existing: PAUSE_BASE
variable_restore_idle_timeout: 0
gcode:
  ##### get user parameters or use default ##### 
  {% set client = printer['gcode_macro _CLIENT_VARIABLE']|default({}) %}
  {% set idle_timeout = client.idle_timeout|default(0) %}
  {% set temp = printer[printer.toolhead.extruder].target if printer.toolhead.extruder != '' else 0%}
  {% set restore = False if printer.toolhead.extruder == ''
              else True  if params.RESTORE|default(1)|int == 1 else False %}
  ##### end of definitions #####
  SET_GCODE_VARIABLE MACRO=RESUME VARIABLE=last_extruder_temp VALUE="{{'restore': restore, 'temp': temp}}"
  # set a new idle_timeout value
  {% if idle_timeout > 0 %}
    SET_GCODE_VARIABLE MACRO=PAUSE VARIABLE=restore_idle_timeout VALUE={printer.configfile.settings.idle_timeout.timeout}
    SET_IDLE_TIMEOUT TIMEOUT={idle_timeout}
  {% endif %}
  PAUSE_BASE
  _TOOLHEAD_PARK_PAUSE_CANCEL {rawparams}

[gcode_macro RESUME]
description: Resume the actual running print
rename_existing: RESUME_BASE
variable_last_extruder_temp: {'restore': False, 'temp': 0}
gcode:
  ##### get user parameters or use default #####
  {% set client = printer['gcode_macro _CLIENT_VARIABLE']|default({}) %}
  {% set velocity = printer.configfile.settings.pause_resume.recover_velocity %}
  {% set sp_move = client.speed_move|default(velocity) %}
  ##### end of definitions #####
  # restore idle_timeout time if needed
  {% if printer['gcode_macro PAUSE'].restore_idle_timeout > 0 %}
    SET_IDLE_TIMEOUT TIMEOUT={printer['gcode_macro PAUSE'].restore_idle_timeout}
  {% endif %}
  {% if printer.idle_timeout.state|upper == "IDLE" %}
    {% if last_extruder_temp.restore %} M109 S{last_extruder_temp.temp} {% endif %}
  {% endif %}
  _CLIENT_EXTRUDE
  RESUME_BASE VELOCITY={params.VELOCITY|default(sp_move)}

# Usage: SET_PAUSE_NEXT_LAYER [ENABLE=[0|1]] [MACRO=<name>]
[gcode_macro SET_PAUSE_NEXT_LAYER]
description: Enable a pause if the next layer is reached
gcode:
  {% set pause_next_layer = printer['gcode_macro SET_PRINT_STATS_INFO'].pause_next_layer %}
  {% set ENABLE = params.ENABLE|default(1)|int != 0 %}
  {% set MACRO = params.MACRO|default(pause_next_layer.call, True) %}
  SET_GCODE_VARIABLE MACRO=SET_PRINT_STATS_INFO VARIABLE=pause_next_layer VALUE="{{ 'enable': ENABLE, 'call': MACRO }}"

# Usage: SET_PAUSE_AT_LAYER [ENABLE=[0|1]] [LAYER=<number>] [MACRO=<name>]
[gcode_macro SET_PAUSE_AT_LAYER]
description: Enable/disable a pause if a given layer number is reached
gcode:
  {% set pause_at_layer = printer['gcode_macro SET_PRINT_STATS_INFO'].pause_at_layer %}
  {% set ENABLE = params.ENABLE|int != 0 if params.ENABLE is defined
             else params.LAYER is defined %}
  {% set LAYER = params.LAYER|default(pause_at_layer.layer)|int %}
  {% set MACRO = params.MACRO|default(pause_at_layer.call, True) %}
  SET_GCODE_VARIABLE MACRO=SET_PRINT_STATS_INFO VARIABLE=pause_at_layer VALUE="{{ 'enable': ENABLE, 'layer': LAYER, 'call': MACRO }}"

# Usage: SET_PRINT_STATS_INFO [TOTAL_LAYER=<total_layer_count>] [CURRENT_LAYER= <current_layer>]
[gcode_macro SET_PRINT_STATS_INFO]
rename_existing: SET_PRINT_STATS_INFO_BASE
description: Overwrite, to get pause_next_layer and pause_at_layer feature
variable_pause_next_layer: { 'enable': False, 'call': "PAUSE" }
variable_pause_at_layer  : { 'enable': False, 'layer': 0, 'call': "PAUSE" }
gcode:
  {% if pause_next_layer.enable %}
    RESPOND TYPE=echo MSG='{"%s, forced by pause_next_layer" % pause_next_layer.call}'
    {pause_next_layer.call} ; execute the given gcode to pause, should be either M600 or PAUSE
    SET_PAUSE_NEXT_LAYER ENABLE=0
  {% elif pause_at_layer.enable and params.CURRENT_LAYER is defined and params.CURRENT_LAYER|int == pause_at_layer.layer %}
    RESPOND TYPE=echo MSG='{"%s, forced by pause_at_layer [%d]" % (pause_at_layer.call, pause_at_layer.layer)}'
    {pause_at_layer.call} ; execute the given gcode to pause, should be either M600 or PAUSE
    SET_PAUSE_AT_LAYER ENABLE=0
  {% endif %}
  SET_PRINT_STATS_INFO_BASE {rawparams}
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

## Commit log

2023-09-30 Config and Macros
    [customMacros.cfg, printer.cfg]
2023-10-12 STL backup
    [2020_spool_holder.stl, 3030_spool_holder.stl, 5015_blower_holder.STL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]
2023-11-16 Quick Update :)
    [CUSTOM_MACROS.cfg, MAINSAIL_MACROS.cfg, PURGE_ARC.cfg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]
